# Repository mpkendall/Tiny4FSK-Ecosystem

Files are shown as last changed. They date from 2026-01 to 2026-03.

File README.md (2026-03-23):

# Tiny4FSK Ecosystem

### A set of additional features, tools, and boards to expand functionality of Tiny4FSK

### TinyShield
TinyShield is an expansion board which sits atop of Tiny4FSK's expansion pins. It adds:
1. An OLED screen for basic flight diagnostics,
2. SD card for logging,
3. 5v logic headers for more sensors,
4. Integrated buck/boost for wider range of power sources, including a LiPo connector,
5. Qwiic headers for adding more sensors!

Code in the Tiny4FSK repository already implements automatic sensor, SD card, and screen scanning and initialization. Functions pertaining to these features are configurable in both `config.h` and the main `Tiny4FSK.ino` file.

To get started, solder female headers to the 2.54mm pins on the back side of the shield. To interface with the Tiny4FSK board, additionally solder 2.54mm male header rows to the USB, power, and data headers on the Tiny4FSK. Mounting them for alignment may assist with soldering.

Insert the shield board onto the Tiny4FSK's headers as shown. No code changes are required to continue with SD card logging and screen initialization.

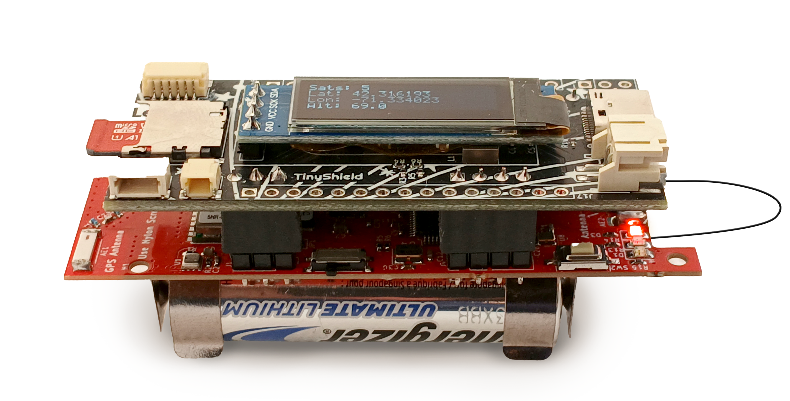
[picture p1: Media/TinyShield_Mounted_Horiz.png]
Boards stacked


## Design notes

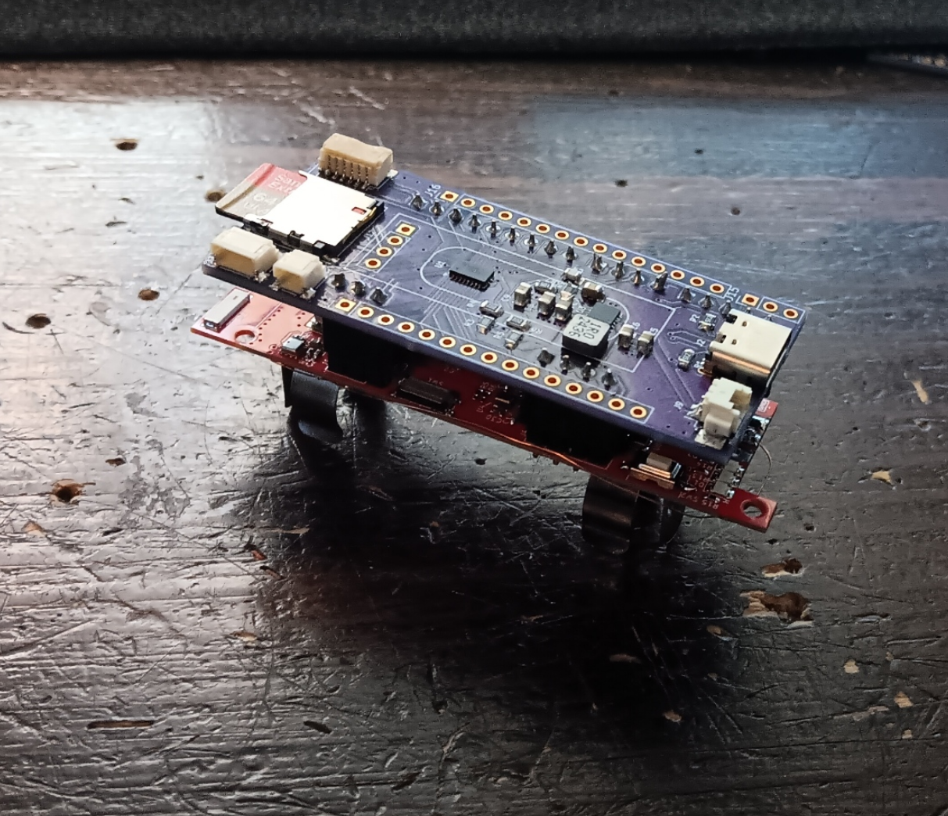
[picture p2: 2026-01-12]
Media/headers.png

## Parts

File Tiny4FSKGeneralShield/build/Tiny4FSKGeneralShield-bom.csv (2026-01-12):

Reference | Value | Footprint | Qty | JLCPCB Part #
C3 | 100nF | Capacitor_SMD:C_0402_1005Metric | 1 | C1525
C4 | 10pF | Capacitor_SMD:C_0402_1005Metric | 1 | C32949
C5 | 10uF | Capacitor_SMD:C_0402_1005Metric | 1 | C15525
C6 | 10uF | Capacitor_SMD:C_0402_1005Metric | 1 | C15525
C7 | 22uF | Capacitor_SMD:C_0603_1608Metric | 1 | C59461
C8 | 22uF | Capacitor_SMD:C_0603_1608Metric | 1 | C59461
C9 | 22uF | Capacitor_SMD:C_0603_1608Metric | 1 | C59461
J1 | Micro_SD_Card | Connector_Card:microSD_HC_Hirose_DM3D-SF | 1 | C719027
J2 | USB_C_Receptacle_USB2.0_14P | Connector_USB:USB_C_Receptacle_GCT_USB4105-xx-A_16P_TopMnt_Horizontal | 1 | C2760486
J5 | Ext.BME280 | Connector_JST:JST_SH_SM04B-SRSS-TB_1x04-1MP_P1.00mm_Horizontal | 1 | C51940130
J9 | Ext.Pwr | Connector_JSt_Extended:HX20007-2AWB | 1 | C442222
J10 | Ext.IMU | Connector_JST:JST_SH_SM06B-SRSS-TB_1x06-1MP_P1.00mm_Horizontal | 1 | C160405
J11 | Ext.Photo | Connector_JST:JST_SH_SM02B-SRSS-TB_1x02-1MP_P1.00mm_Horizontal | 1 | C160402
L1 | 1uH | Inductor_Extended:IND_SRP4020FA-1R0M | 1 | C842935
R1 | 5.1kR | Resistor_SMD:R_0402_1005Metric | 1 | C25905
R2 | 5.1kR | Resistor_SMD:R_0402_1005Metric | 1 | C25905
R3 | 1kR | Resistor_SMD:R_0402_1005Metric | 1 | C11702
R4 | 2kR | Resistor_SMD:R_0402_1005Metric | 1 | C4109
R5 | 1kR | Resistor_SMD:R_0402_1005Metric | 1 | C11702
R6 | 2kR | Resistor_SMD:R_0402_1005Metric | 1 | C4109
R7 | 1M | Resistor_SMD:R_0402_1005Metric | 1 | C26083
R9 | 111kR | Resistor_SMD:R_0805_2012Metric | 1 | C865144
U1 | FXMA108 | Package_DFN_QFN:WQFN-20-1EP_2.5x4.5mm_P0.5mm_EP1x2.9mm | 1 | C891320
U3 | TPS63060 | Package_SON:Texas_S-PWSON-N10_ThermalVias | 1 | C48567

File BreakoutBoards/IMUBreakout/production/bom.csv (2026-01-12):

Designator | Footprint | Quantity | Value | LCSC Part #
C1, C2 | 0402 | 2 | 1uF | C52923
C5, C6 | 0402 | 2 | 100nF | C1525
J10 | JST_SH_SM06B-SRSS-TB_1x06-1MP_P1.00mm_Horizontal | 1 | IMU Connection | C160405
J5 | JST_SH_SM04B-SRSS-TB_1x04-1MP_P1.00mm_Horizontal | 1 | Qwicc | C51940130
R1, R2 | 0402 | 2 | 4.7k | C25900
U1 | Bosch_LGA-14_3x2.5mm_P0.5mm | 1 | ICM-42607-P | C5129967

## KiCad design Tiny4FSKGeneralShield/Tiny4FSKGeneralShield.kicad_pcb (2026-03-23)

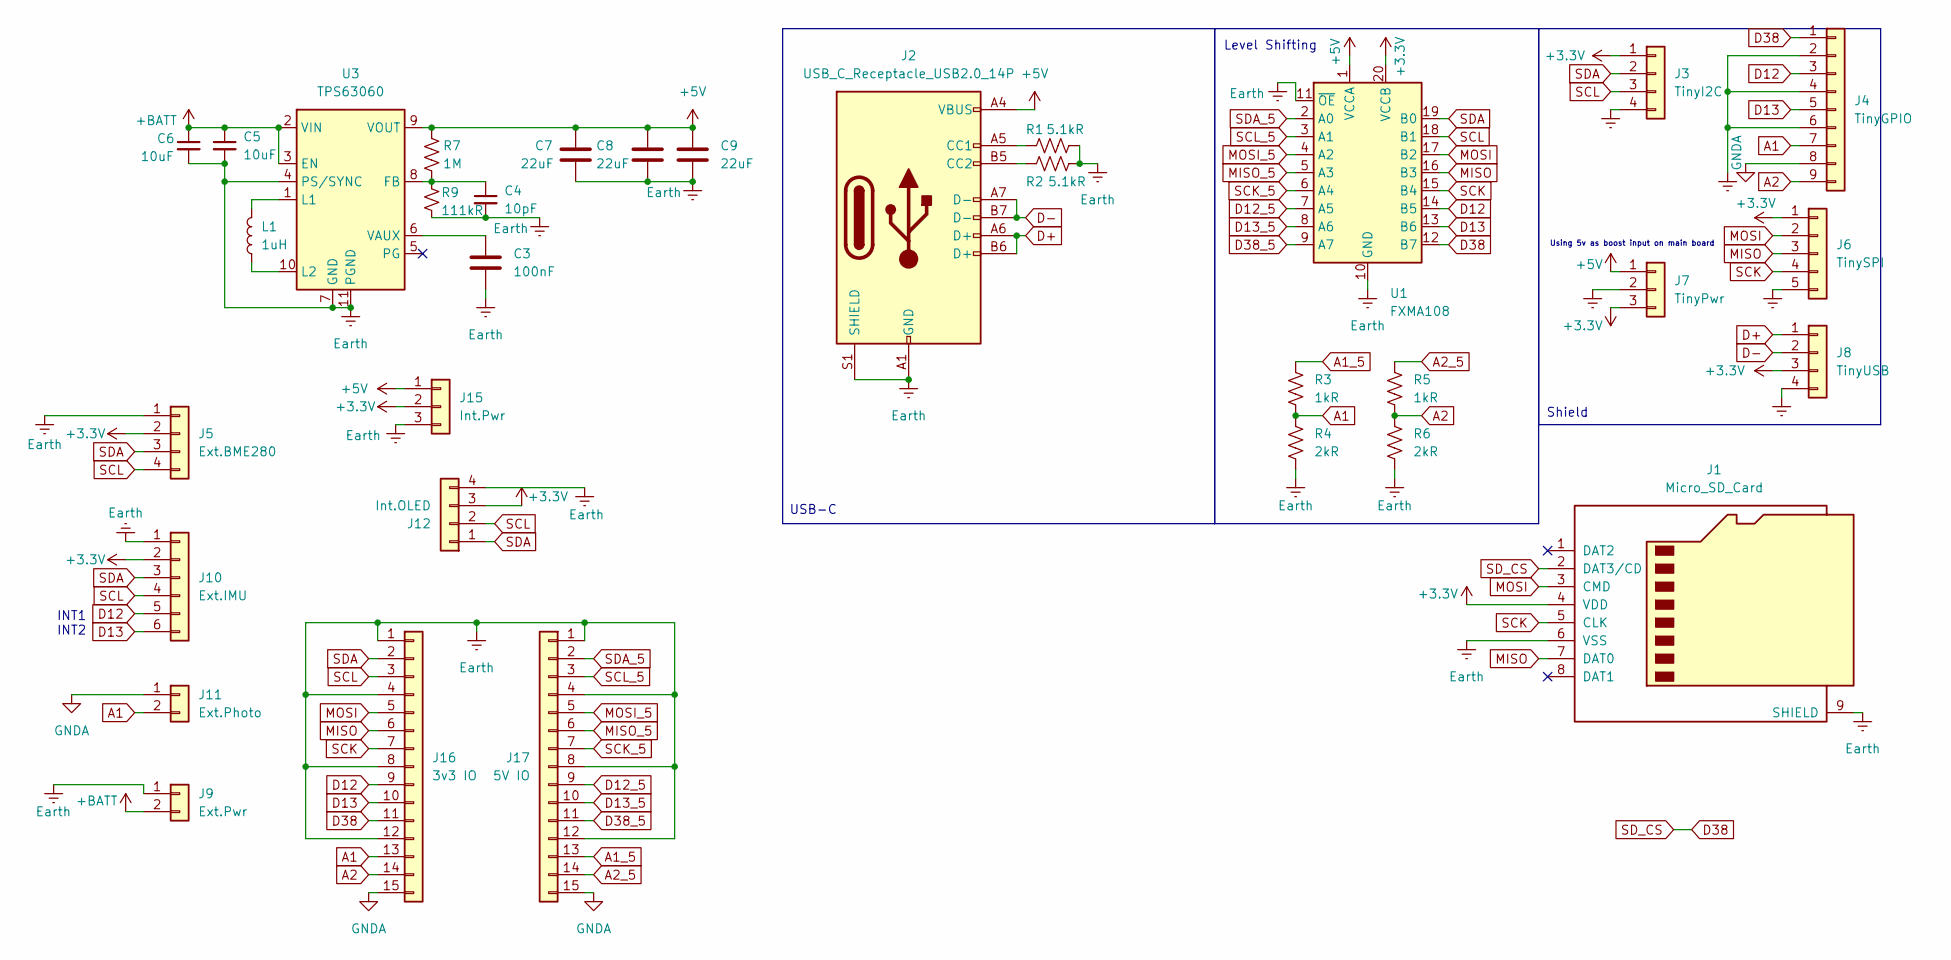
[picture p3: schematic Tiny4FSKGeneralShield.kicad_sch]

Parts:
C3: 100nF; C_0402_1005Metric; JLCPCB Part # C1525
C4: 10pF; C_0402_1005Metric; JLCPCB Part # C32949
C5, C6: 10uF; C_0402_1005Metric; JLCPCB Part # C15525
C7, C8, C9: 22uF; C_0603_1608Metric; JLCPCB Part # C59461
J1: Micro_SD_Card; microSD_HC_Hirose_DM3D-SF; JLCPCB Part # C719027
J2: USB_C_Receptacle_USB2.0_14P; USB_C_Receptacle_GCT_USB4105-xx-A_16P_TopMnt_Horizontal; JLCPCB Part # C2760486
J3: TinyI2C; PinSocket_1x04_P2.54mm_Vertical
J4: TinyGPIO; PinSocket_1x09_P2.54mm_Vertical
J5: Ext.BME280; JST_SH_SM04B-SRSS-TB_1x04-1MP_P1.00mm_Horizontal; JLCPCB Part # C51940130
J6: TinySPI; PinSocket_1x05_P2.54mm_Vertical
J7: TinyPwr; PinSocket_1x03_P2.54mm_Vertical
J8: TinyUSB; PinSocket_1x04_P2.54mm_Vertical
J9: Ext.Pwr; HX20007-2AWB; JLCPCB Part # C442222
J10: Ext.IMU; JST_SH_SM06B-SRSS-TB_1x06-1MP_P1.00mm_Horizontal; JLCPCB Part # C160405
J11: Ext.Photo; JST_SH_SM02B-SRSS-TB_1x02-1MP_P1.00mm_Horizontal; JLCPCB Part # C160402
J12: Int.OLED; PinHeader_1x04_P2.54mm_Vertical
J15: Int.Pwr; PinHeader_1x03_P2.54mm_Vertical
J16: 3v3 IO; PinHeader_1x15_P2.54mm_Vertical
J17: 5V IO; PinHeader_1x15_P2.54mm_Vertical
L1: 1uH; IND_SRP4020FA-1R0M; JLCPCB Part # C842935
R1, R2: 5.1kR; R_0402_1005Metric; JLCPCB Part # C25905
R3, R5: 1kR; R_0402_1005Metric; JLCPCB Part # C11702
R4, R6: 2kR; R_0402_1005Metric; JLCPCB Part # C4109
R7: 1M; R_0402_1005Metric; JLCPCB Part # C26083
R9: 111kR; R_0805_2012Metric; JLCPCB Part # C865144
U1: FXMA108; WQFN-20-1EP_2.5x4.5mm_P0.5mm_EP1x2.9mm; JLCPCB Part # C891320
U3: TPS63060; Texas_S-PWSON-N10_ThermalVias; JLCPCB Part # C48567

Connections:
+3.3V: J1.4 (VDD), J3.1, J5.2, J6.1, J7.3, J8.3, J10.2, J12.3, J15.2, U1.20 (VCCB)
+5V: C7.1, C8.1, C9.1, J2.A4 (VBUS), J2.A9 (VBUS), J2.B4 (VBUS), J2.B9 (VBUS), J7.1, J15.1, R7.1, U1.1 (VCCA), U3.9 (VOUT)
+BATT: C5.1, C6.1, J9.2, U3.2 (VIN), U3.3 (EN)
A1: J4.7, J11.2, J16.13, R3.2, R4.1
A1_5: J17.13, R3.1
A2: J4.9, J16.14, R5.2, R6.1
A2_5: J17.14, R5.1
D12: J4.3, J10.5, J16.9, U1.14 (B5)
D12_5: J17.9, U1.7 (A5)
D13: J4.5, J10.6, J16.10, U1.13 (B6)
D13_5: J17.10, U1.8 (A6)
D38: J1.2 (DAT3/CD), J4.1, J16.11, U1.12 (B7)
D38_5: J17.11, U1.9 (A7)
D+: J2.A6 (D+), J2.B6 (D+), J8.1
D-: J2.A7 (D-), J2.B7 (D-), J8.2
Earth: C3.2, C4.2, C5.2, C6.2, C7.2, C8.2, C9.2, J1.6 (VSS), J1.9 (SHIELD), J2.A1 (GND), J2.A12 (GND), J2.B1 (GND), J2.B12 (GND), J2.S1 (SHIELD), J3.4, J4.2, J4.4, J4.6, J5.1, J6.5, J7.2, J8.4, J9.1, J10.1, J12.4, J15.3, J16.1, J16.4, J16.8, J16.12, J17.1, J17.4, J17.8, J17.12, R1.2, R2.2, R4.2, R6.2, R9.2, U1.10 (GND), U1.11 (~OE), U3.4 (PS/SYNC), U3.7 (GND), U3.11 (PGND)
GNDA: J4.8, J11.1, J16.15, J17.15
MISO: J1.7 (DAT0), J6.3, J16.6, U1.16 (B3)
MISO_5: J17.6, U1.5 (A3)
MOSI: J1.3 (CMD), J6.2, J16.5, U1.17 (B2)
MOSI_5: J17.5, U1.4 (A2)
unnamed: J2.A5 (CC1), R1.1
unnamed: J2.B5 (CC2), R2.1
unnamed: C4.1, R7.2, R9.1, U3.8 (FB)
unnamed: L1.2, U3.1 (L1)
unnamed: L1.1, U3.10 (L2)
unnamed: C3.1, U3.6 (VAUX)
SCK: J1.5 (CLK), J6.4, J16.7, U1.15 (B4)
SCK_5: J17.7, U1.6 (A4)
SCL: J3.3, J5.4, J10.4, J12.2, J16.3, U1.18 (B1)
SCL_5: J17.3, U1.3 (A1)
SDA: J3.2, J5.3, J10.3, J12.1, J16.2, U1.19 (B0)
SDA_5: J17.2, U1.2 (A0)

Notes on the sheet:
Level Shifting
USB-C
INT1 INT2
Using 5v as boost input on main board
Shield

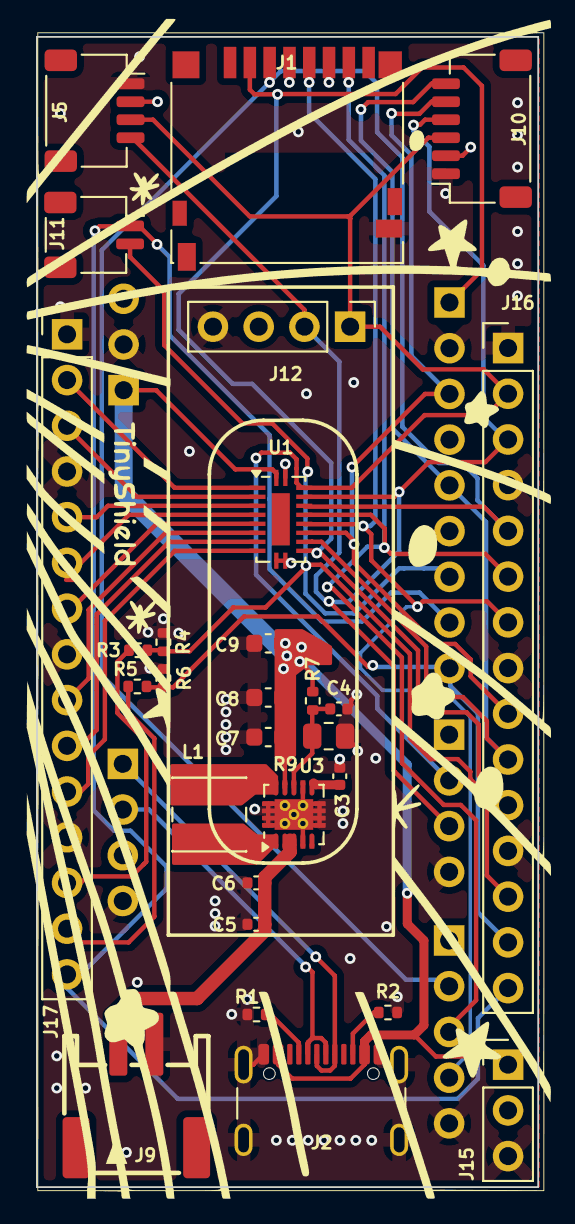
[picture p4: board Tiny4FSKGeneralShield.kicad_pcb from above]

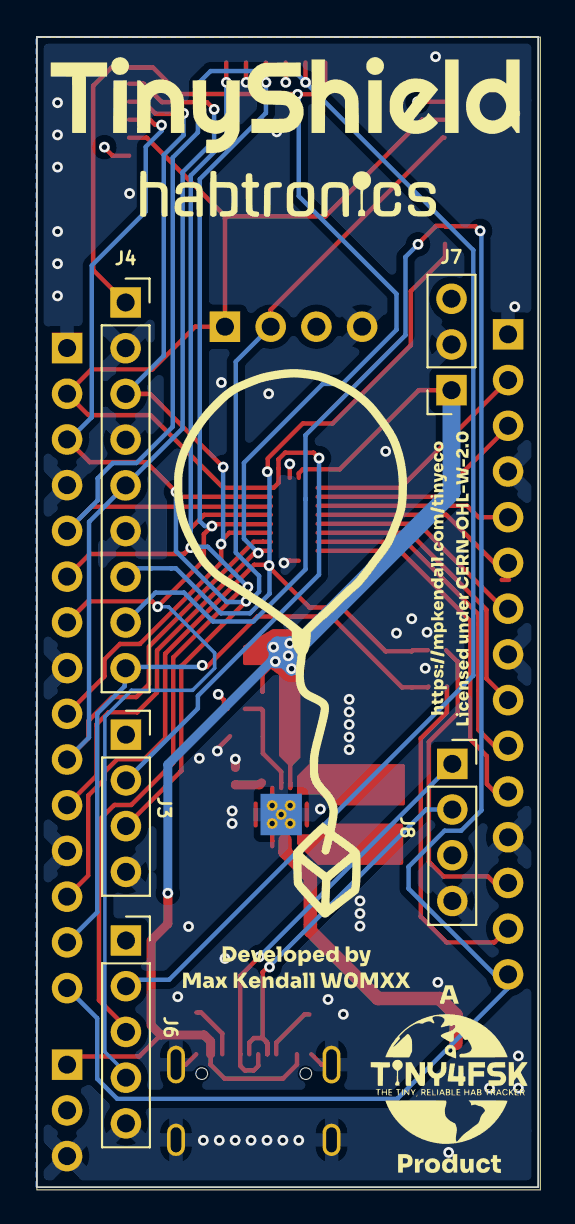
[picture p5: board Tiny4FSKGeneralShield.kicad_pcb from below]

Board: 4 copper layers, 27.9 x 63.9 mm, 33 parts (5 on the bottom side), 33 nets.

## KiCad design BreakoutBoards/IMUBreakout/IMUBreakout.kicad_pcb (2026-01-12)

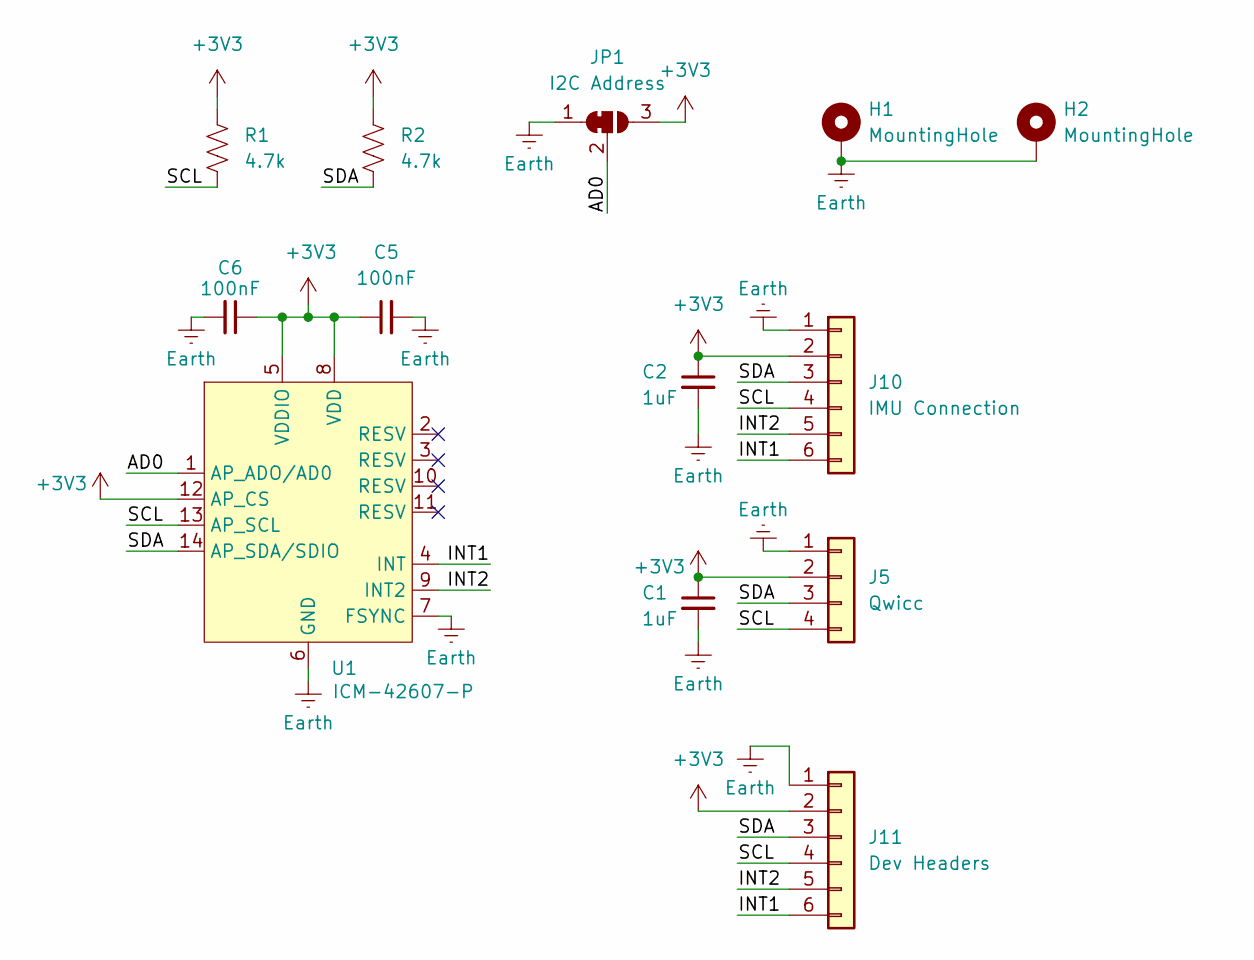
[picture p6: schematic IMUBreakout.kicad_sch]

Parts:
C1, C2: 1uF; C_0402_1005Metric; LCSC C52923
C5, C6: 100nF; C_0402_1005Metric; LCSC C1525
H1, H2: MountingHole; MountingHole_2.2mm_M2_Pad_Via
J5: Qwicc; JST_SH_SM04B-SRSS-TB_1x04-1MP_P1.00mm_Horizontal; LCSC C51940130
J10: IMU Connection; JST_SH_SM06B-SRSS-TB_1x06-1MP_P1.00mm_Horizontal; LCSC C160405
J11: Dev Headers; PinSocket_1x06_P2.54mm_Vertical
JP1: I2C Address; SolderJumper-3_P1.3mm_Bridged12_RoundedPad1.0x1.5mm
R1, R2: 4.7k; R_0402_1005Metric; LCSC C25900
U1: ICM-42607-P; Bosch_LGA-14_3x2.5mm_P0.5mm; LCSC C5129967

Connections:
+3V3: C1.1, C2.1, C5.1, C6.1, J5.2, J10.2, J11.2, JP1.3 (B), R1.1, R2.1, U1.5 (VDDIO), U1.8 (VDD), U1.12 (AP_CS)
/AD0: JP1.2 (C), U1.1 (AP_ADO/AD0)
/INT1: J10.6, J11.6, U1.4 (INT)
/INT2: J10.5, J11.5, U1.9 (INT2)
/SCL: J5.4, J10.4, J11.4, R1.2, U1.13 (AP_SCL)
/SDA: J5.3, J10.3, J11.3, R2.2, U1.14 (AP_SDA/SDIO)
Earth: C1.2, C2.2, C5.2, C6.2, H1.1, H2.1, J5.1, J10.1, J11.1, JP1.1 (A), U1.6 (GND), U1.7 (FSYNC)

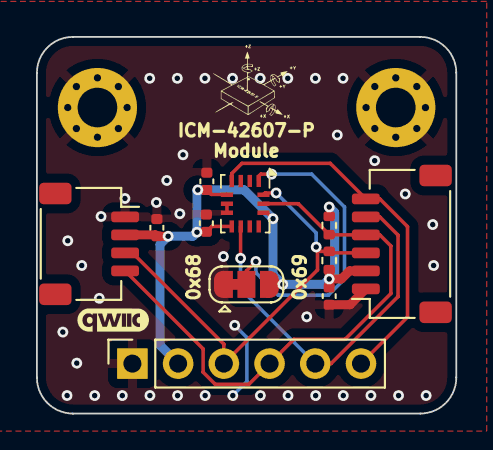
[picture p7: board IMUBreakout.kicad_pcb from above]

Board: 2 copper layers, 23.3 x 20.9 mm, 13 parts (0 on the bottom side), 7 nets.

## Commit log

2025-11-03 ugh it got overwritten
    [Tiny4FSKGeneralShield.kicad_pcb, Tiny4FSKGeneralShield.kicad_sch]
2025-11-04 starting to get caught up
    [Tiny4FSKGeneralShield.kicad_pcb]
2025-11-11 need to find jlc part for qwiic
    [Tiny4FSKGeneralShield.kicad_pcb, Tiny4FSKGeneralShield.kicad_sch]
2025-11-13 release candidate!
    [Tiny4FSKGeneralShield.kicad_pcb, Tiny4FSKGeneralShield.kicad_sch]
2026-01-04 update pcb
    [IMUBreakout.kicad_pcb, IMUBreakout.kicad_sch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]
2026-01-12 updated IMU board and production files
    [IMUBreakout.kicad_pcb, IMUBreakout.kicad_sch, Tiny4FSKGeneralShield-bom.csv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]
2026-03-23 kicad 10
    [Tiny4FSKGeneralShield.kicad_pcb, Tiny4FSKGeneralShield.kicad_sch]
